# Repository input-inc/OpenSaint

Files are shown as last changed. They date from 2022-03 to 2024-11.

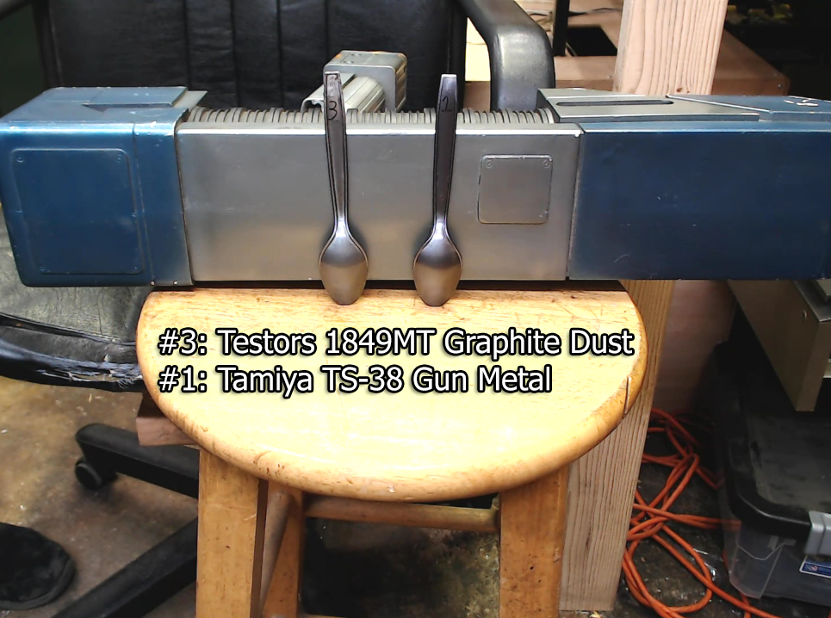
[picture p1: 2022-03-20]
J5 Project/Current CAD/Resources/Manufacturing & Helpful Info/J5 Paint (002).png

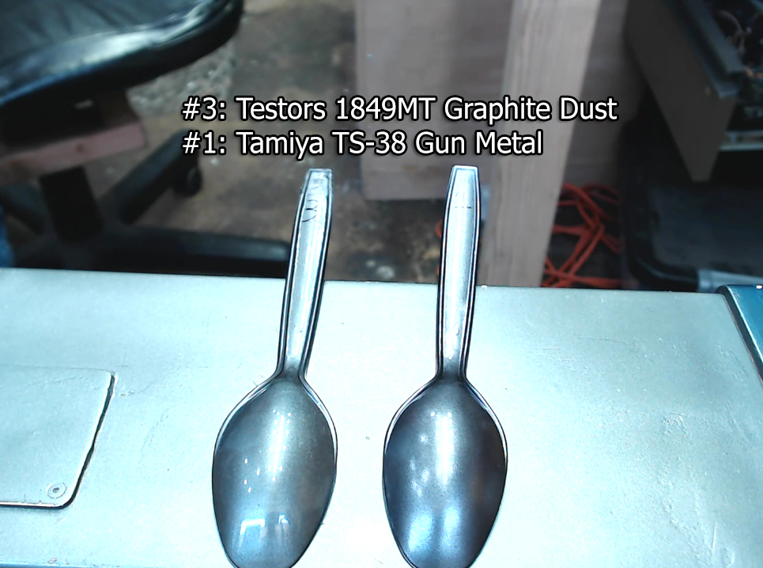
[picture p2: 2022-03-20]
J5 Project/Current CAD/Resources/Manufacturing & Helpful Info/J5 Paint (001).png

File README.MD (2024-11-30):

Input-Inc logo Header
# Welcome to OpenSAINT by Input-Inc.

OpenSAINT is a robotic platform that is a screen accurate replica of a well known movie robot. This platform represents years of mechanical design and collaboration by the Input-Inc. team. Except where noted, it is not affiliated with any persons or groups outside of its core team. Please visit our website (www.input-inc.com) for more information. Please familiarize yourself with this document before proceeding. Building a full-size OpenSAINT robot is an expensive, laborious, and time consuming process. It is recommended you have machining experience, and experience building RC controlled systems.

## Help Keep this Project ALIVE!
We've been working on this project for over twenty years, and have countless hours poured into it. We use industrial grade software and tools to bring this project to an international community of builders, and we can only continue our efforts with your help. Through our Patreon we offer several tiers for builders and non-builders alike to support the project. [Check out our Patreon](https://www.patreon.com/inputinc/)

## License Terms & Conditions
These files are provided under a Creative Commons Attribution-NonCommercial-ShareAlike 4.0 International license (included), and as such this information, or derivatives thereof are intended solely for personal use and cannot be used for commercial purposes. Any distributed modifications of this information must be done under the same terms, and include the license of the original work. 

# !! WARNING !!
Before you get started be warned that this robot when built to specification can still be dangerous. Certain safety mechanisms or mechanical considerations have been designed to reduce this risk as much as possible but the design contains multiple high-powered motors, servos, and mechanisms that in their normal operation can injure the operator or bystanders. It is not recommend to run this robot without taking proper precautions to protect those within its field of operation. 

# How to get started

## Getting the current CAD
Before you download the CAD we recommend you read through our [CAD Releases](https://github.com/input-inc/OpenSaint/wiki/CAD-Releases) document. This will give you more information on our release schedules, distribution mechanisms, and recommended software. Always be sure you have the newest version of the CAD before building, and always get your CAD from the Input-Inc. GitHub repository or Patreon.

## Downloading the CAD from GitHub
GitHub is a public source control hosting and management platform. We use it to host our public CAD. For those without Git experience we recommend downloading the [Git Desktop](https://desktop.github.com) client, and using that to download the files. This will ensure that the LFS structure of the repository is retained when you download it. You will need at least 10GB of hard drive space available to download the entire CAD. 

**!! Do not use the 'Download ZIP' option in the Code dropdown on the GitHub website. That will not download the file contents !!** 
### GitHub Desktop Steps
1. Download GitHub Desktop for your operating system.
2. Install it. (For macOS open the zip file and drag the application to your `/Applications` folder.)
3. Open GitHub Desktop.
4. Select the `File` menu and select `Clone Repository`.
5. Select the `URL` tab from the dialog.
6. Enter this URL: `https://github.com/input-inc/OpenSaint.git`
7. Choose a location where you want to save the files. **IMPORTANT:** For Windows you must install at the top level of a drive like C:, because the path names will exceed the Windows maximum length if it is installed elsewhere.
8. Click the `Clone` button.
9. Wait for the repository to finish downloading.

### Git Command-line Steps
If you prefer to use the command line it will require current versions of `git` and `git lfs`. Download and install in whatever way is appropriate for your operating system.
1. `git lfs clone <repository URL> <path to save>`

## Reading the CAD

### What software do I need?
#### CAD
These CAD files are provided in SolidWorks format and we **expressly** recommend using SolidWorks to read them as outlined in our [CAD Releases](https://github.com/input-inc/OpenSaint/wiki/CAD-Releases) document. To get SolidWorks:Maker, (an affordable version of SolidWorks) you can follow the steps in our [SolidWorks Guide](https://github.com/input-inc/OpenSaint/wiki/Installing-3DExperience-SolidWorks-for-Makers).

Some software packages like Fusion 360 may only read the solid data from the file and could exclude part configurations or other details. Unless otherwise provided, parts do not include flat patterns specified for sheet metal manufacturing. An understanding of CAD tools will be required to extract usable dimensions and patterns for manufacturing.

#### Markdown
For reading the MD (Markdown) files within the repository on your desktop (you can always read them natively within Git's web interface), you'll need a compatible markdown viewer. Here are some suggestions:

##### macOS
- [The 6 Best Mac Markdown Editors](https://www.makeuseof.com/tag/mac-markdown-editors/)

##### Windows
- [The 4 Best Markdown Editors for Windows](https://www.makeuseof.com/best-markdown-editors-windows/)

## How is the CAD organized
The major sections of the robot are broken into folders and subfolders for sub-assemblies. Part files are named to make locating them within this structure as easy as possible. For example the file named: `[CRDL-COMN-C-COMN-00] Battery box.SLDPRT` , could be found at the following path:

`ROOT > [04 CRDL] Cradle Base > [ COMN] Common > [C] Battery Box > [ COMN] Common`

### Configurations and build options (ex. v1 vs. v2)
Input-Inc. uses a few ways to denote differing configurations of assemblies and part files. For certain parts a SolidWorks configuration is provided to represent earlier valid versions of the part, as we endeavor to retain backwards compatibility wherever possible. Be sure to check the configurations tab in SolidWorks to see the differing versions. For some assemblies a V1 or V2 folder can be found within the folder structure to illustrate differing approaches to building the assembly. Not all versions of all assemblies may be compatible so use caution when deviating from the default configurations.

## What you’ll need
Building OpenSAINT will require a full suite of tools, and in many cases we suggest having machining capabilities yourself to build these parts. It is strongly recommended that you fully train and familiarize yourself with any machine or tool outlined here. We accept no responsibility for injuries sustained or failed parts from improper use of these tools.

### Machines
For these machines we recommend the largest you can afford and realistically own.
- Mill (Bench top or larger)
- Lathe (Capable of cutting metal) (Bench top or larger)
- 3D printer (FDM: 350mm2 minimum recommended, Resin)

### Tools
Fractional and Metric allen wrench sets - Most of the fasteners on OpenSAINT are fractional size socket head cap screws. We recommend a quality set of these that go down to .028” and 0.7mm

## Vendors
Most off-the-shelf parts included in the CAD include part numbers for ease of searching. 

### Fasteners
- [McMaster-Carr](https://www.mcmaster.com) - Unless otherwise specified, most of the fasteners can be found here. 
- [Bolt Depot](https://boltdepot.com)
- [Fastenal](fastenal.com)

### Laser cutting
For laser cut parts we’ve found the following vendors to provide excellent results:

- [SendCutSend](https://sendcutsend.com) - 2D sheet metal, laser cutting, and some bending.
- [OSHCut](https://www.oshcut.com) - 2D sheet metal, laser cutting, and bending
- [Ponoko](https://www.ponoko.com) - Plastics laser cutting

### PCBs
- [JLPCB](https://jlpcb.com)
- [OSH Park](https://oshpark.com)
- [PCBWay](https://pcbway.com)

### Servos
- [Servo City](https://www.servocity.com) - Motors, servos, gears
- [ASME](https://www.aliexpress.com/item/32975864627.html) - Beware knock-offs. This is our recommended vendor.

### 3D Printing
- [CraftCloud](https://craftcloud3d.com) - A large marketplace for 3D printing services.

### Other Vendors
- [Bearings Direct](https://bearingsdirect.com)
- [MetalsDepot](https://www.metalsdepot.com)

## Where to get parts
- Part runs - Occasionally Input-Inc. members will have parts for sale, or do parts runs. Visit our [Facebook](https://www.facebook.com/groups/inputinc) and check the announcements for parts runs. We do our best to ensure fit and compatibility but you may still need to make adjustments on stuff.
- [OpenSAINT part Inventory](https://docs.google.com/spreadsheets/d/1wjoVz0FKgDMVw29Vhd8r6FyhR2xi7lMMy8atvSe49dA/edit?usp=sharing) - [Ramon](ryvarra@cyberantics.net) has a running inventory of parts from previous runs and general collecting. Check the list and contact through the Facebook group or by email to make a purchase. Keep in mind that inventory purchases are limited to Patreon Builder/Pro Builder members.

## Community resources
Join us on our Facebook group, and always be on the lookout for build videos.
- [Facebook](https://www.facebook.com/groups/inputinc)
- [YouTube](https://www.youtube.com/user/J5GURU)

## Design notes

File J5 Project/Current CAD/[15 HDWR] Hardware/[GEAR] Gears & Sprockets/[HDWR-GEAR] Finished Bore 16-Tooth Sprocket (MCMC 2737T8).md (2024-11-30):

# @
| Attribute | Value |
| ---  | --- |
| Author | hackmancoltaire |
| Date | 09/27/2016 |
| Part Type | Purchased |
| Cost | 31.04 |
| _SW_Last_Saved_With_ | SOLIDWORKS 2024 |
# Stock
| Attribute | Value |
| ---  | --- |
| Description | Finshed Bore 16-Tooth Sprocket (MCMC 2737T8, Stock) |
| Author | hackmancoltaire |
| Date | 09/27/2016 |
| Part Type | Purchased |
| Cost | 31.04 |
# TUPR Neck Drive
| Attribute | Value |
| ---  | --- |
| Description | BORED SPROCKET. 3/16&quot;Keyway, with Set Screws |
| Comment | https://ametric.com/product/59430/25b1612 |
| Author | hackmancoltaire |
| Date | 09/27/2016 |
| Number | 300936 |
| Part Type | Purchased |
| Cost | 31.04 |
# Neck Drive
| Attribute | Value |
| ---  | --- |
| Description | Finshed Bore 16-Tooth Sprocket (MCMC 2737T8, TUPR Neck Drive) |
| Author | hackmancoltaire |
| Date | 09/27/2016 |
| Part Type | Purchased |
| Cost | 31.04 |

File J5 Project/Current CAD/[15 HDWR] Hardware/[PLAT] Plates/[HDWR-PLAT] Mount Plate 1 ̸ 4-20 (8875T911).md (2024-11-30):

# @
| Attribute | Value |
| ---  | --- |
| Project Name |  |
| Description | Mount Plate for 1/4&quot;-20 Thread Size |
| Author | hackmancoltaire |
| Project number |  |
| Date | 10/16/2024 |
| Number | 8875T911 |
| Vendor | McMaster-Carr Supply Company |
| Material | Steel |
| Part Type | Purchased |
| Cost | 1.28/5 |
| _SW_Last_Saved_With_ | SOLIDWORKS 2024 |
# 8875T911
| Attribute | Value |
| ---  | --- |
| Project Name |  |
| Author | hackmancoltaire |
| Project number |  |
| Date | 10/16/2024 |
| Part Type | Purchased |
| Cost | 1.28/5 |

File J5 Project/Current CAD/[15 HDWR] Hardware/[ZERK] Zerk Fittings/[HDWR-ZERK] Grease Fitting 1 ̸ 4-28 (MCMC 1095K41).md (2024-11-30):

# @
| Attribute | Value |
| ---  | --- |
| Project Name |  |
| Description | Zinc-Plated Steel Grease Fitting |
| Author | hackmancoltaire |
| Project number |  |
| Date | 11/09/2024 |
| Vendor | McMaster-Carr Supply Company |
| Material | Steel |
| _SW_Last_Saved_With_ | SOLIDWORKS 2024 |
# Default
| Attribute | Value |
| ---  | --- |
| Project Name |  |
| Author | hackmancoltaire |
| Project number |  |
| Date | 11/09/2024 |

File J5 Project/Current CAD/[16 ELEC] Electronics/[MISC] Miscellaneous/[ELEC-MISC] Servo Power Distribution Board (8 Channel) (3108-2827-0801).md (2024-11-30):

# @
| Attribute | Value |
| ---  | --- |
| Project Name |  |
| Description | Servo Power Distribution Board (8 Channel) |
| Author | hackmancoltaire |
| Project number |  |
| Date | 11/02/2024 |
| Number | 3108-2827-0801 |
| Vendor | GoBuilda |
| _SW_Last_Saved_With_ | SOLIDWORKS 2024 |
# Default
| Attribute | Value |
| ---  | --- |
| Project Name |  |
| Author | hackmancoltaire |
| Project number |  |
| Date | 11/02/2024 |
| Vendor | GoBuilda |

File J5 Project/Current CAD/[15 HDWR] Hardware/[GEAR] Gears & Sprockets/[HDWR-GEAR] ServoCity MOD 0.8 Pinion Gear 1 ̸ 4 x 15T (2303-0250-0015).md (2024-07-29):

# @
| Attribute | Value |
| ---  | --- |
| Project Name |  |
| Description | 2303 Series Steel, MOD 0.8 Pinion Gear (1/4&quot; Round Bore, 15 Tooth) |
| Author | hackmancoltaire |
| Revision | ANY |
| Project number |  |
| Date | 07/28/2024 |
| Number | 2303-0250-0015 |
| Vendor | ServoCity |
| Part Type | Purchased |
| Cost | 9.99 |
| _SW_Last_Saved_With_ | SOLIDWORKS 2024 |
# Default
| Attribute | Value |
| ---  | --- |
| Project Name |  |
| Author | hackmancoltaire |
| Project number |  |
| Date | 07/28/2024 |
| Vendor | ServoCity |
| Part Type | Purchased |
| Cost | 9.99 |

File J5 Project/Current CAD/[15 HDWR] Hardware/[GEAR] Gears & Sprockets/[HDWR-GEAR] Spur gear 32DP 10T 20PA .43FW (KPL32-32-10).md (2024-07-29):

# @
| Attribute | Value |
| ---  | --- |
| Project Name |  |
| Description | 10T, 0.125&quot; (1/8) Bore 32P Shaft Mount Pinion Gear (Steel) |
| Author | hackmancoltaire |
| Project number |  |
| Date | 06/22/2024 |
| Number | KPL32-32-10 |
| Part Type | Purchased |
| Cost | 5.99 |
| _SW_Last_Saved_With_ | SOLIDWORKS 2024 |
# Default
| Attribute | Value |
| ---  | --- |
| Project Name |  |
| Author | hackmancoltaire |
| Project number |  |
| Date | 06/22/2024 |
| Part Type | Purchased |
| Cost | 5.99 |

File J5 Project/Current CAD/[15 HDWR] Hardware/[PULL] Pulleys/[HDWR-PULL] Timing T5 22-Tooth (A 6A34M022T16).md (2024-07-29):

# @
| Attribute | Value |
| ---  | --- |
| Author | hackmancoltaire |
| Date | 11/30/2019 |
| _SW_Last_Saved_With_ | SOLIDWORKS 2024 |
# ARM Hug Output
| Attribute | Value |
| ---  | --- |
| Author | hackmancoltaire |
| Date | 11/30/2019 |
# ARM Hug Servo
| Attribute | Value |
| ---  | --- |
| Author | hackmancoltaire |
| Date | 11/30/2019 |

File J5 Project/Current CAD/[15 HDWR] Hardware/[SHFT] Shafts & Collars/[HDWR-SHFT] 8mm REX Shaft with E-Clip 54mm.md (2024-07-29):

# @
| Attribute | Value |
| ---  | --- |
| Project Name |  |
| Description | 8mm REX™ Shaft with E-Clip (Stainless Steel, 54mm Length) |
| Author | hackmancoltaire |
| Revision | ANY |
| Project number |  |
| Date | 07/14/2024 |
| Number | 2106-4008-0540 |
| Part Type | Purchased |
| Cost | 3.79 |
| _SW_Last_Saved_With_ | SOLIDWORKS 2024 |
# Default
| Attribute | Value |
| ---  | --- |
| Project Name |  |
| Author | hackmancoltaire |
| Project number |  |
| Date | 07/14/2024 |
| Part Type | Purchased |
| Cost | 3.79 |

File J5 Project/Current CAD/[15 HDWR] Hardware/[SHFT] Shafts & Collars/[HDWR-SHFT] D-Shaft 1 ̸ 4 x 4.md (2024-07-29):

# @
| Attribute | Value |
| ---  | --- |
| Project Name |  |
| Description | 1/4&quot; D-Shaft (Stainless Steel, 4&quot; Length) |
| Author | hackmancoltaire |
| Project number |  |
| Date | 06/23/2024 |
| Number | 2101-1250-0400 |
| Vendor | ServoCity |
| Part Type | Purchased |
| Cost | 3.89 |
| _SW_Last_Saved_With_ | SOLIDWORKS 2024 |
# Default
| Attribute | Value |
| ---  | --- |
| Project Name |  |
| Author | hackmancoltaire |
| Project number |  |
| Date | 06/23/2024 |
| Vendor | ServoCity |
| Part Type | Purchased |
| Cost | 3.89 |

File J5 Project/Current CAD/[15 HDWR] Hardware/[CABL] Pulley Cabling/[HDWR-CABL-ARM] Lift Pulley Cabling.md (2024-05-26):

# @
| Attribute | Value |
| ---  | --- |
| Description | 18-8 Stainless Steel Corrosion-Resistant Wire Rope |
| Author | hackmancoltaire |
| Date | 02/21/2016 |
| Number | 3461T474 |
| Part Type | Purchased |
| _SW_Last_Saved_With_ | SOLIDWORKS 2024 |
# Default
| Attribute | Value |
| ---  | --- |
| Author | hackmancoltaire |
| Date | 02/21/2016 |
| Part Type | Purchased |

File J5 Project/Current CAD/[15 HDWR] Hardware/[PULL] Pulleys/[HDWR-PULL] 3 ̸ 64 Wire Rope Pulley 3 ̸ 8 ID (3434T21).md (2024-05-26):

# @
| Attribute | Value |
| ---  | --- |
| Description | Pulley for Wire Rope |
| Author | hackmancoltaire |
| Date | 11/05/2023 |
| Number | 3434T21 |
| Vendor | McMaster-Carr Supply Company |
| Material | Steel |
| Part Type | Purchased |
| Cost | 4.90 |
| _SW_Last_Saved_With_ | SOLIDWORKS 2024 |
# 3434T21
| Attribute | Value |
| ---  | --- |
| Author | hackmancoltaire |
| Date | 11/05/2023 |
| Part Type | Purchased |
| Cost | 4.90 |

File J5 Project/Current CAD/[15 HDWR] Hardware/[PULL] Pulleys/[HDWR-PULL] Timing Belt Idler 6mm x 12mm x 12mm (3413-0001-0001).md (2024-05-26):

# @
| Attribute | Value |
| ---  | --- |
| Description | Acetal Timing Belt Idler |
| Author | hackmancoltaire |
| Revision | ANY |
| Date | 11/28/2022 |
| Number | 3413-0001-0001 |
| Part Type | Purchased |
| Cost | 2.99/2 |
| _SW_Last_Saved_With_ | SOLIDWORKS 2024 |
# Default
| Attribute | Value |
| ---  | --- |
| Author | hackmancoltaire |
| Date | 11/28/2022 |
| Part Type | Purchased |
| Cost | 2.99/2 |

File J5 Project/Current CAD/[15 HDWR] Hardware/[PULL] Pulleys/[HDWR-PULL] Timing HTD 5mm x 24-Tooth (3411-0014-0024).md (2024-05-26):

# @
| Attribute | Value |
| ---  | --- |
| Description | 5mm HTD Pitch Aluminum Hub Mount Timing Belt Pulley (14mm Bore, 24 Tooth) |
| Author | hackmancoltaire |
| Date | 11/28/2022 |
| Number | 3411-0014-0024 |
| Part Type | Purchased |
| Cost | 7.99 |
| _SW_Last_Saved_With_ | SOLIDWORKS 2024 |
# Default
| Attribute | Value |
| ---  | --- |
| Author | hackmancoltaire |
| Date | 11/28/2022 |
| Part Type | Purchased |
| Cost | 7.99 |

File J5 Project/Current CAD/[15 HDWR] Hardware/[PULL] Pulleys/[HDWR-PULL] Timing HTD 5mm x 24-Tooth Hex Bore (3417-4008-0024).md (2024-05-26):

# @
| Attribute | Value |
| ---  | --- |
| Description | 5mm HTD Pitch Set Screw Pinion Timing Belt Pulley (8mm REX Bore, 24 Tooth) |
| Author | hackmancoltaire |
| Date | 11/29/2022 |
| Number | 3417-4008-0024 |
| Part Type | Purchased |
| Cost | 8.99 |
| _SW_Last_Saved_With_ | SOLIDWORKS 2024 |
# Default
| Attribute | Value |
| ---  | --- |
| Author | hackmancoltaire |
| Date | 11/29/2022 |
| Part Type | Purchased |
| Cost | 8.99 |

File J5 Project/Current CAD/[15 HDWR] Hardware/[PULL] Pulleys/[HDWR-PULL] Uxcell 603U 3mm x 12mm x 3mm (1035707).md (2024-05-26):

# @
| Attribute | Value |
| ---  | --- |
| Project Name |  |
| Description | Uxcell 603 U Groove Ball Track Guide Bearing 3x10x3mm Double Metal Shielded (GCr15) Chrome Steel Bearing |
| Author | hackmancoltaire |
| Project number |  |
| Date | 04/14/2024 |
| Number | 1035707 |
| Part Type | Purchased |
| Cost | 6.08/2 |
| _SW_Last_Saved_With_ | SOLIDWORKS 2024 |
# Default
| Attribute | Value |
| ---  | --- |
| Project Name |  |
| Author | hackmancoltaire |
| Project number |  |
| Date | 04/14/2024 |
| Part Type | Purchased |
| Cost | 6.08/2 |

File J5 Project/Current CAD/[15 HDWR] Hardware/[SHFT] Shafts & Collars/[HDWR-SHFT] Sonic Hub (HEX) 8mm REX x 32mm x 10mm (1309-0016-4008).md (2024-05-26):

# @
| Attribute | Value |
| ---  | --- |
| Description | Sonic Hub (8mm REX Bore) |
| Author | hackmancoltaire |
| Date | 11/28/2022 |
| Number | 1309-0016-4008 |
| _SW_Last_Saved_With_ | SOLIDWORKS 2024 |
# Stock
| Attribute | Value |
| ---  | --- |
| Author | hackmancoltaire |
| Date | 11/28/2022 |
# Arm - Inner
| Attribute | Value |
| ---  | --- |
| Author | hackmancoltaire |
| Date | 11/28/2022 |
# Arm - Outer
| Attribute | Value |
| ---  | --- |
| Author | hackmancoltaire |
| Date | 11/28/2022 |

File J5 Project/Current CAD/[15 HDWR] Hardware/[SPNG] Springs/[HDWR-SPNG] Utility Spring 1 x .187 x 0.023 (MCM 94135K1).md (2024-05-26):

# @
| Attribute | Value |
| ---  | --- |
| Project Name |  |
| Description | 302 Stainless Steel Corrosion-Resistant Extension Spring |
| Author | hackmancoltaire |
| Project number |  |
| Date | 04/28/2024 |
| Number | 94135K1 |
| Vendor | McMaster-Carr Supply Company |
| Material | 302 Stainless Steel |
| _SW_Last_Saved_With_ | SOLIDWORKS 2024 |
# 94135K1
| Attribute | Value |
| ---  | --- |
| Project Name |  |
| Author | hackmancoltaire |
| Project number |  |
| Date | 04/28/2024 |

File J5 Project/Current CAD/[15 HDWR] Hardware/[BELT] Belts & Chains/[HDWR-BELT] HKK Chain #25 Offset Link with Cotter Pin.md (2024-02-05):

# @
| Attribute | Value |
| ---  | --- |
| Project Name |  |
| Description | Adding-and-Connecting Link for ANSI Number 25-SS Single Strand Corrosion-Resistant Roller Chain |
| Author | hackmancoltaire |
| Project number |  |
| Date | 01/14/2024 |
| Number | 6264K3 |
| Vendor | McMaster-Carr Supply Company |
| Material | 304 Stainless Steel |
| _SW_Last_Saved_With_ | SOLIDWORKS 2024 |
# 6264K3
| Attribute | Value |
| ---  | --- |
| Project Name |  |
| Author | hackmancoltaire |
| Project number |  |
| Date | 01/14/2024 |

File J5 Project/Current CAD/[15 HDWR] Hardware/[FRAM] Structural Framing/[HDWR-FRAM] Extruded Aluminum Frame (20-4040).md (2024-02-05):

# @
| Attribute | Value |
| ---  | --- |
| Project Name |  |
| Description | 40mm X 40mm T-Slotted Profile - Eight Open T-Slots |
| Author | hackmancoltaire |
| Project number |  |
| Date | 02/04/2024 |
| Number | 20-4040 |
| Part Type | Purchased |
| Cost | .0285/mm |
| _SW_Last_Saved_With_ | SOLIDWORKS 2024 |
# Default
| Attribute | Value |
| ---  | --- |
| Project Name |  |
| Author | hackmancoltaire |
| Project number |  |
| Date | 02/04/2024 |
| Part Type | Purchased |
| Cost | .0285/mm |

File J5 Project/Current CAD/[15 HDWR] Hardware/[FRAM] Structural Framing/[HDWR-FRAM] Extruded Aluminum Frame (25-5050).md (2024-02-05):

# @
| Attribute | Value |
| ---  | --- |
| Project Name |  |
| Description | 50mm X 50mm T-Slotted Profile - Eight Open T-Slots |
| Author | hackmancoltaire |
| Project number |  |
| Date | 01/07/2024 |
| Number | 25-5050 |
| Part Type | Purchased |
| Cost | $0.0330/mm |
| _SW_Last_Saved_With_ | SOLIDWORKS 2024 |
# 111.125mm
| Attribute | Value |
| ---  | --- |
| Project Name |  |
| Author | hackmancoltaire |
| Project number |  |
| Date | 01/07/2024 |
| Part Type | Purchased |
| Cost | $0.0330/mm |
# 51.7525mm
| Attribute | Value |
| ---  | --- |
| Project Name |  |
| Author | hackmancoltaire |
| Project number |  |
| Date | 01/07/2024 |
| Part Type | Purchased |
| Cost | $0.0330/mm |
# 93.6625mm
| Attribute | Value |
| ---  | --- |
| Project Name |  |
| Author | hackmancoltaire |
| Project number |  |
| Date | 01/07/2024 |
| Part Type | Purchased |
| Cost | $0.0330/mm |
# 95.25mm
| Attribute | Value |
| ---  | --- |
| Author | hackmancoltaire |
| Date | 01/07/2024 |
| Part Type | Purchased |
| Cost | $0.0330/mm |
# 52.4002mm
| Attribute | Value |
| ---  | --- |
| Author | hackmancoltaire |
| Date | 01/07/2024 |
| Part Type | Purchased |
| Cost | $0.0330/mm |
# 104.14mm
| Attribute | Value |
| ---  | --- |
| Author | hackmancoltaire |
| Date | 01/07/2024 |
| Part Type | Purchased |
| Cost | $0.0330/mm |
# 49.149mm
| Attribute | Value |
| ---  | --- |
| Author | hackmancoltaire |
| Date | 01/07/2024 |
| Part Type | Purchased |
| Cost | $0.0330/mm |

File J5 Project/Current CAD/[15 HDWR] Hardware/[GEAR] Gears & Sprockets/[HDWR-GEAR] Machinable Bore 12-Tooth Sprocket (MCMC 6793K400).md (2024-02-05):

# @
| Attribute | Value |
| ---  | --- |
| Description | McMaster-Carr ANSI 25 Chain, 12 Teeth, for 1/4&quot; Shaft Diameter |
| Author | SixWingedFreak |
| Date | 09/20/2016 |
| Number | 6793K400 |
| _SW_Last_Saved_With_ | SOLIDWORKS 2024 |
# Stock
| Attribute | Value |
| ---  | --- |
| Author | SixWingedFreak |
| Date | 09/20/2016 |
# TUPR Neck Drive
| Attribute | Value |
| ---  | --- |
| Author | SixWingedFreak |
| Date | 09/20/2016 |

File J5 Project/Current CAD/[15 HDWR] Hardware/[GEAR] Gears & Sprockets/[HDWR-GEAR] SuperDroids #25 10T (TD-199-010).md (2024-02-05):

# @
| Attribute | Value |
| ---  | --- |
| Project Name |  |
| Description | Steel D-Shaft Sprocket for #25 Pitch Chain - 10 Teeth |
| Author | hackmancoltaire |
| Project number |  |
| Date | 01/10/2024 |
| Number | TD-199-010 |
| Part Type | Purchased |
| Cost | 8.64 |
| _SW_Last_Saved_With_ | SOLIDWORKS 2024 |
# 25-0.25P1ST10T10SN3.0H2.0L0.1250N
| Attribute | Value |
| ---  | --- |
| Project Name |  |
| Author | hackmancoltaire |
| Project number |  |
| Date | 01/10/2024 |
| Part Type | Purchased |
| Cost | 8.64 |

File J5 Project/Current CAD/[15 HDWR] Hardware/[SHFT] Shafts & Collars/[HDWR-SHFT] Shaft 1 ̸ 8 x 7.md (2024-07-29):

# @
| Attribute | Value |
| ---  | --- |
| Project Name |  |
| Description | 0.125” (1/8”) x 7.00” Stainless Steel Precision Shafting |
| Author | hackmancoltaire |
| Project number |  |
| Date | 06/19/2024 |
| Number | 634126 |
| Part Type | Purchased |
| Cost | 1.19 |
| _SW_Last_Saved_With_ | SOLIDWORKS 2024 |
# Default
| Attribute | Value |
| ---  | --- |
| Project Name |  |
| Author | hackmancoltaire |
| Project number |  |
| Date | 06/19/2024 |
| Part Type | Purchased |
| Cost | 1.19 |

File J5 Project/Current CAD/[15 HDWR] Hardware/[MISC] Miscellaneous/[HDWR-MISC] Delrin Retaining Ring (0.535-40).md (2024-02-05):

# @
| Attribute | Value |
| ---  | --- |
| Project Name |  |
| Description | Retaining Ring 0.535-40 Thread (Pack Of 10) |
| Author | hackmancoltaire |
| Project number |  |
| Date | 01/29/2024 |
| Number | RR05-P10 |
| Part Type | Purchased |
| Cost | 38.50/10 |
| _SW_Last_Saved_With_ | SOLIDWORKS 2024 |
# Default
| Attribute | Value |
| ---  | --- |
| Project Name |  |
| Author | hackmancoltaire |
| Project number |  |
| Date | 01/29/2024 |
| Part Type | Purchased |
| Cost | 38.50/10 |
# Simplified
| Attribute | Value |
| ---  | --- |
| Project Name |  |
| Author | hackmancoltaire |
| Project number |  |
| Date | 01/29/2024 |
| Part Type | Purchased |
| Cost | 38.50/10 |

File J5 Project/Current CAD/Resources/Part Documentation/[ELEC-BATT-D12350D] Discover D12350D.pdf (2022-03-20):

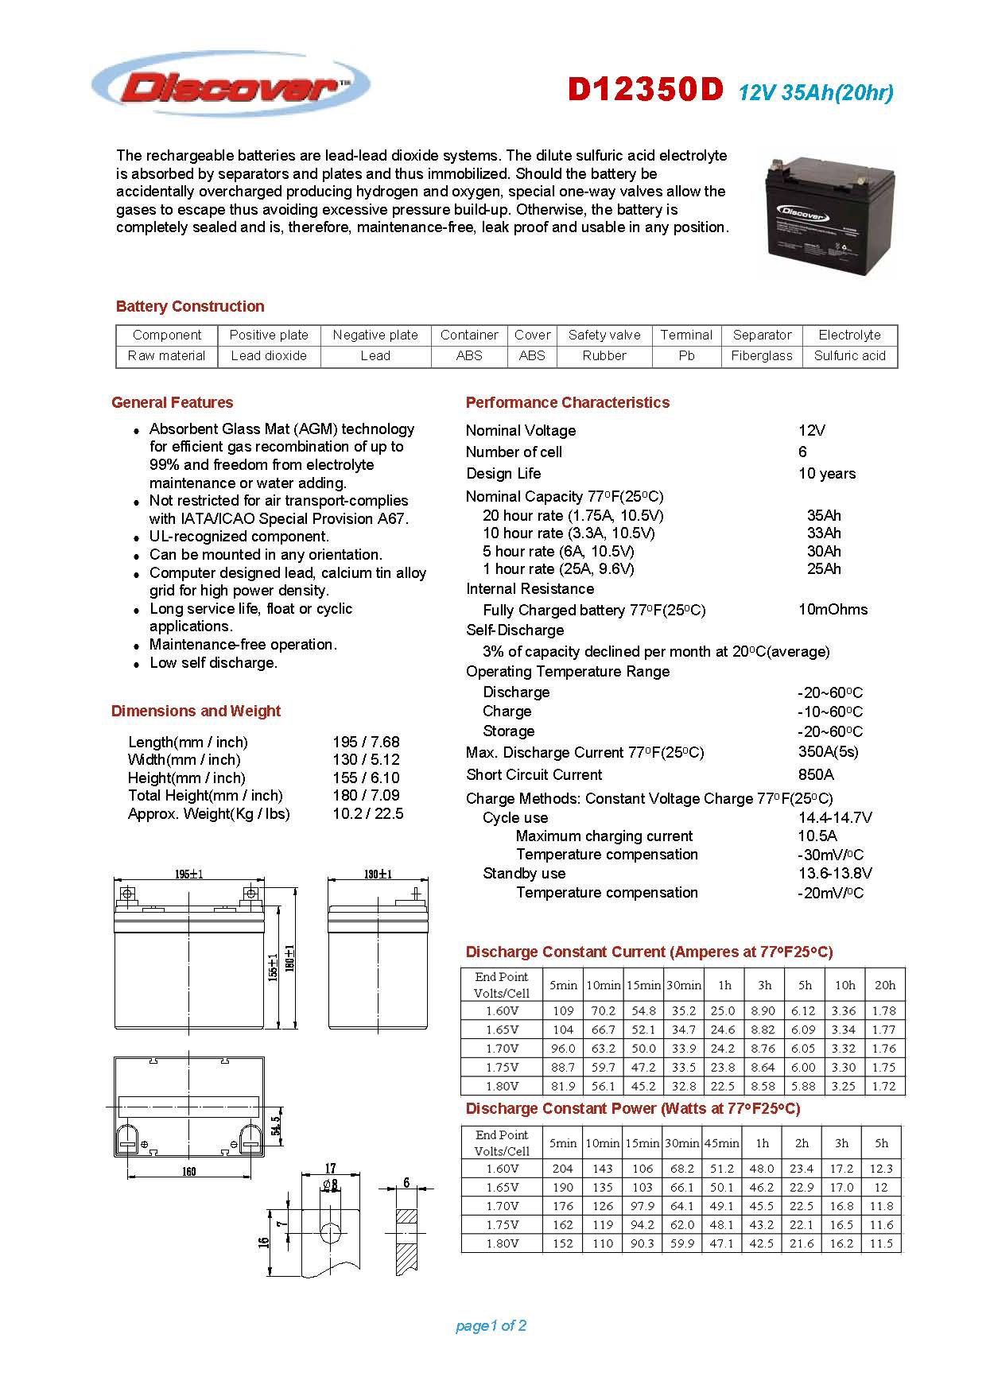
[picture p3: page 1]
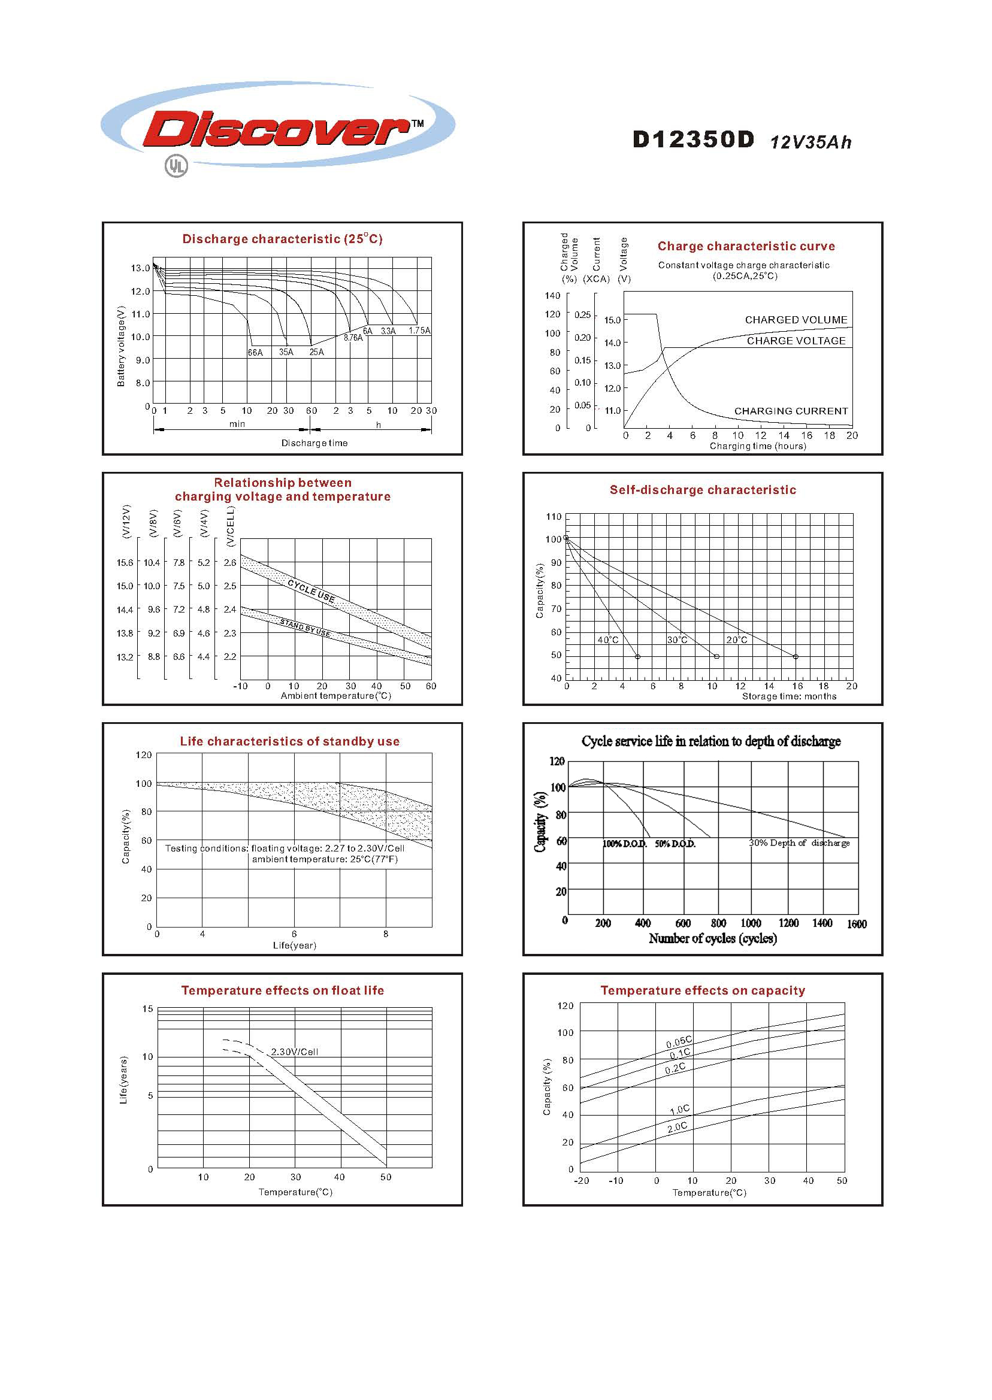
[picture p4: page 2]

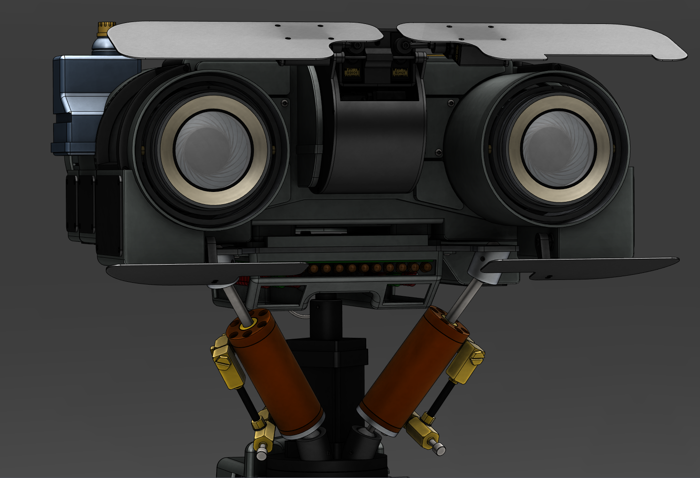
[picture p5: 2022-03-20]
J5 Project/Current CAD/Resources/Renders & Screenshots/Head01.png

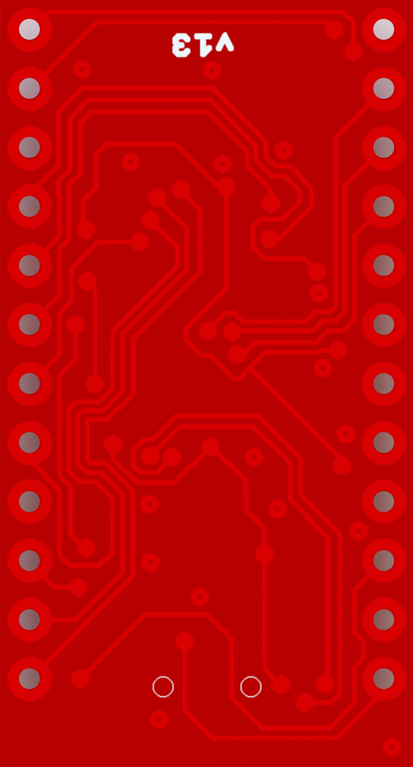
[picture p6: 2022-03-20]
J5 Project/Current CAD/Resources/Decals/PCBs/Arduino Pro Micro PCB (Bottom).png

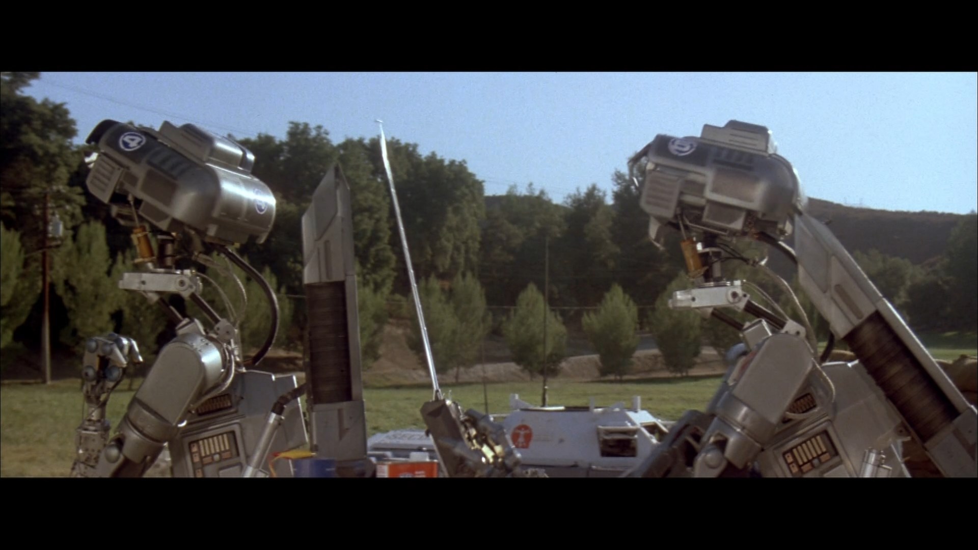
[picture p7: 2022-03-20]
J5 Project/Current CAD/[13 ACC] Accessory/[LASR] Laser/[ MSTR] Master/Reference/Laser Reference 32.jpg

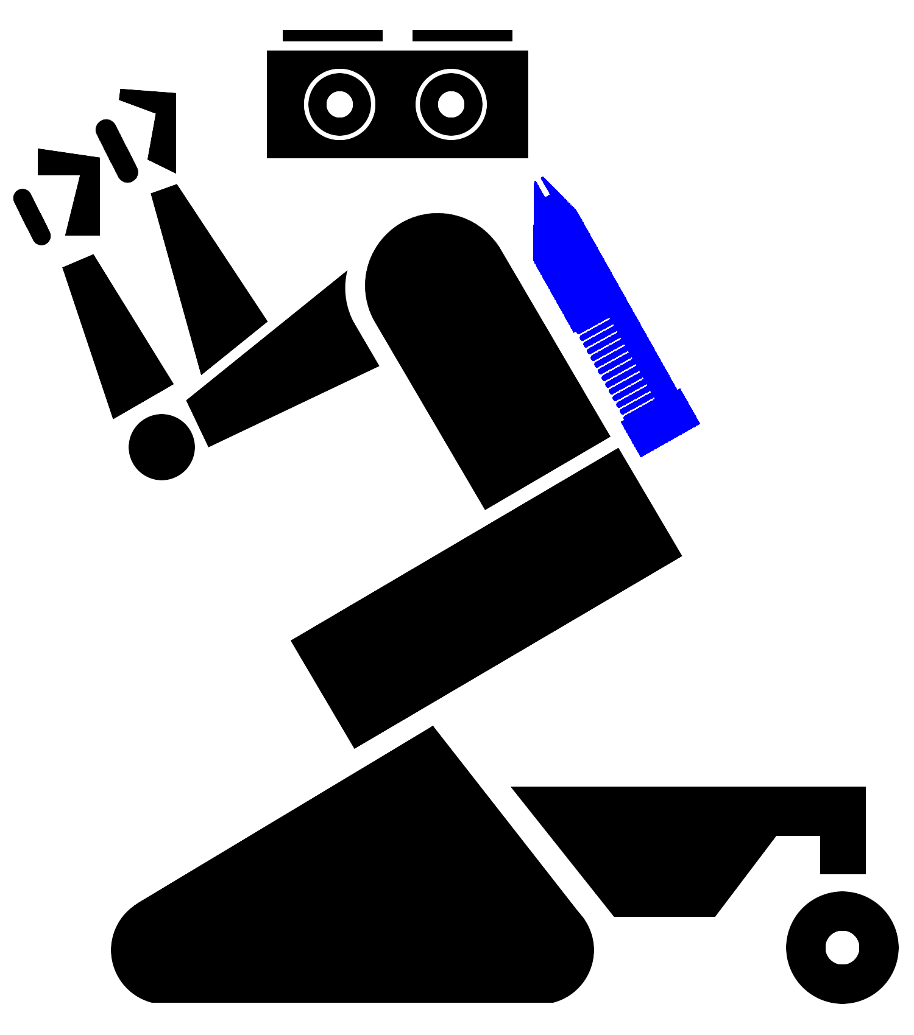
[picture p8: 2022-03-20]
J5 Project/Current CAD/Resources/SolidWorks Settings & Tools/Drawing Resources/Art/Zones/ACC.png

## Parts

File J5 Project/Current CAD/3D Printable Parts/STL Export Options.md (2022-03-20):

# 
| Attribute | Value |
| ---  | --- |
| Author | SixWingedFreak |
| Width | 944 |
| Height | 810 |
| Color Depth | 8 |

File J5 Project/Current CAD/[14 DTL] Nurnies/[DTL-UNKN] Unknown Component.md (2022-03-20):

# @
| Attribute | Value |
| ---  | --- |
| Author | SixWingedFreak |
| Date | 05/19/2015 |
# Chamfered Corners
| Attribute | Value |
| ---  | --- |
| Author | SixWingedFreak |
| Date | 05/19/2015 |
# Rounded Corners
| Attribute | Value |
| ---  | --- |
| Author | SixWingedFreak |
| Date | 05/19/2015 |

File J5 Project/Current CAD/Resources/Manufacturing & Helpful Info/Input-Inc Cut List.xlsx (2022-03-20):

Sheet: Standard
INPUT-INC CUT LIST
DESCRIPTION | SIZE | CUTS | TOTAL REQUIRED | PURCHASE | BREAKDOWN
90° Angle Steel | 1¼" x 1¼" | 11.25'' | 11.25'' | 1' x1 | N/A
 | ¾" x ¾" | 22.16'' | 44.32'' | 6' x1 | N/A
 |  | 22.16''
 | ½" x ½" | 13.8'' | 89.155'' | 3' x1 6' x1 | 3' 4.965" x2 3.875 x2 1.6875" x1
 |  | 13.8''
 |  | 10.25''
 |  | 10.25''
 |  | 5''
 |  | 5''
 |  | 5''
 |  | 5'' |  |  | 6' 13.8" x2 10.25" x2 5" x4 1.6875" x1
 |  | 4.965''
 |  | 4.965''
 |  | 3.875''
 |  | 3.875''
 |  | 1.6875''
 |  | 1.6875''
90° Angle Aluminum | ¾" x ¾" | 5'' | 14.75'' | 3' x1 | N/A
 |  | 5''
 |  | 2''
 |  | 2''
 |  | 0.375''
 |  | 0.375''

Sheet: Terry
INPUT-INC CUT LIST (TERRY)
DESCRIPTION | SIZE | CUTS | TOTAL REQUIRED | PURCHASE | BREAKDOWN
90° Angle Steel | 1¼" x 1¼" | 11.25'' | 11.25'' | 1' x1 | N/A
 | ¾" x ¾" | 22.16'' | 59.07'' | 6' x1 | N/A
 |  | 22.16''
 |  | 5''
 |  | 5''
 |  | 2''
 |  | 2''
 |  | 0.375''
 |  | 0.375''
 | ½" x ½" | 13.8'' | 89.155'' | 3' x1 6' x1 | 3' 4.965" x2 3.875 x2 1.6875" x1
 |  | 13.8''
 |  | 10.25''
 |  | 10.25''
 |  | 5''
 |  | 5''
 |  | 5''
 |  | 5'' |  |  | 6' 13.8" x2 10.25" x2 5" x4 1.6875" x1
 |  | 4.965''
 |  | 4.965''
 |  | 3.875''
 |  | 3.875''
 |  | 1.6875''
 |  | 1.6875''

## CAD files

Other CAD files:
J5 Project/Current CAD/[00 FULL] Complete Assembly/[ COMN] Common/[FULL-COMN] Lower Half.SLDASM
J5 Project/Current CAD/[00 FULL] Complete Assembly/[FULL] Complete Assembly.SLDASM
J5 Project/Current CAD/[01 HEAD] Head (UNFINISHED)/[ COVR] Coverings/[MIL1] Facemask & Mouthguard/[HEAD-COVR-MIL1] Facemask & Mouthguard Assembly.SLDASM
J5 Project/Current CAD/[01 HEAD] Head (UNFINISHED)/[A] Shell/[HEAD-A] Top Shell.SLDASM
J5 Project/Current CAD/[01 HEAD] Head (UNFINISHED)/[B] Eye/[A] Wollensak Raptar 209mm Copy Lens/[HEAD-B-A] Wollensak Raptar 209mm Copy Lens.SLDASM
J5 Project/Current CAD/[01 HEAD] Head (UNFINISHED)/[B] Eye/[C] Iris Rotator/[HEAD-B-C] Iris Rotator.SLDASM
J5 Project/Current CAD/[01 HEAD] Head (UNFINISHED)/[B] Eye/[D] XY Eye Articulator/[HEAD-B-D-R] XY Eye Articulator (Right).SLDASM
J5 Project/Current CAD/[01 HEAD] Head (UNFINISHED)/[B] Eye/[HEAD-B] Eye.SLDASM
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

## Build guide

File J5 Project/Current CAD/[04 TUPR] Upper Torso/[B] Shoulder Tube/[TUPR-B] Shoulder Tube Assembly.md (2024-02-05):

# @
| Attribute | Value |
| ---  | --- |
| Author | SixWingedFreak |
| Date | 07/31/2016 |
| _SW_Last_Saved_With_ | SOLIDWORKS 2024 |
# Flipped motor nuts (Screen Accurate)
| Attribute | Value |
| ---  | --- |
| Author | SixWingedFreak |
| Date | 07/31/2016 |
# Symmetric Motor Nuts
| Attribute | Value |
| ---  | --- |
| Author | SixWingedFreak |
| Date | 07/31/2016 |

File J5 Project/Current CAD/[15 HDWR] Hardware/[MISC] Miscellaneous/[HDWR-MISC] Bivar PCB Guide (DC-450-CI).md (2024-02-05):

# @
| Attribute | Value |
| ---  | --- |
| Project Name |  |
| Description | Circuit Board Hardware, PCB Card Guides, DC |
| Author | hackmancoltaire |
| Project number |  |
| Date | 01/26/2024 |
| Number | DC-450-CI |
| Part Type | Purchased |
| _SW_Last_Saved_With_ | SOLIDWORKS 2024 |
# Default
| Attribute | Value |
| ---  | --- |
| Project Name |  |
| Author | hackmancoltaire |
| Project number |  |
| Date | 01/26/2024 |
| Part Type | Purchased |

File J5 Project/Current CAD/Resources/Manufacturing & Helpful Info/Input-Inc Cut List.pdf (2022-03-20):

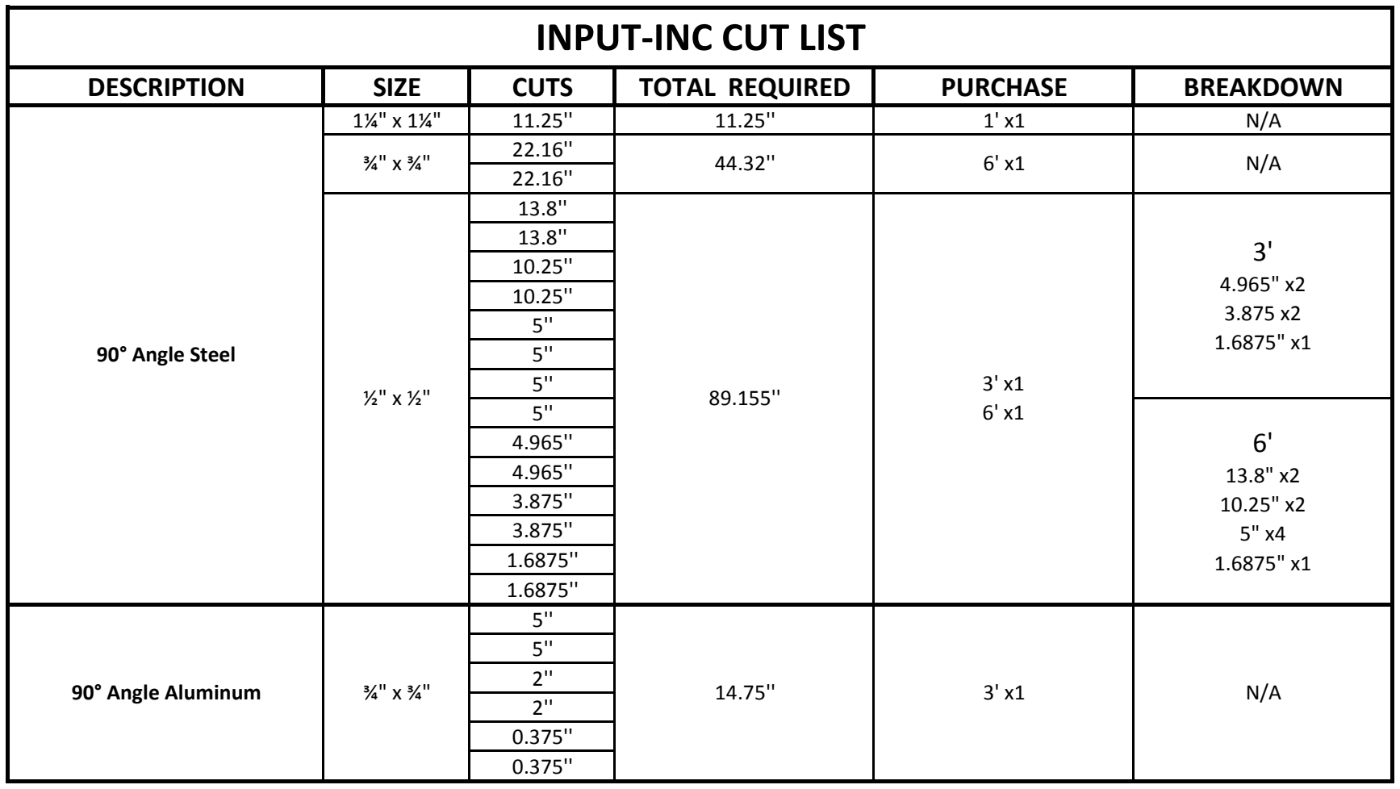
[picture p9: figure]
INPUT-INC CUT LIST; 90° Angle Steel

DESCRIPTION | SIZE | CUTS | TOTAL REQUIRED | PURCHASE | BREAKDOWN
90° Angle Aluminum | ¾" x ¾" | 14.75'' | 3' x1

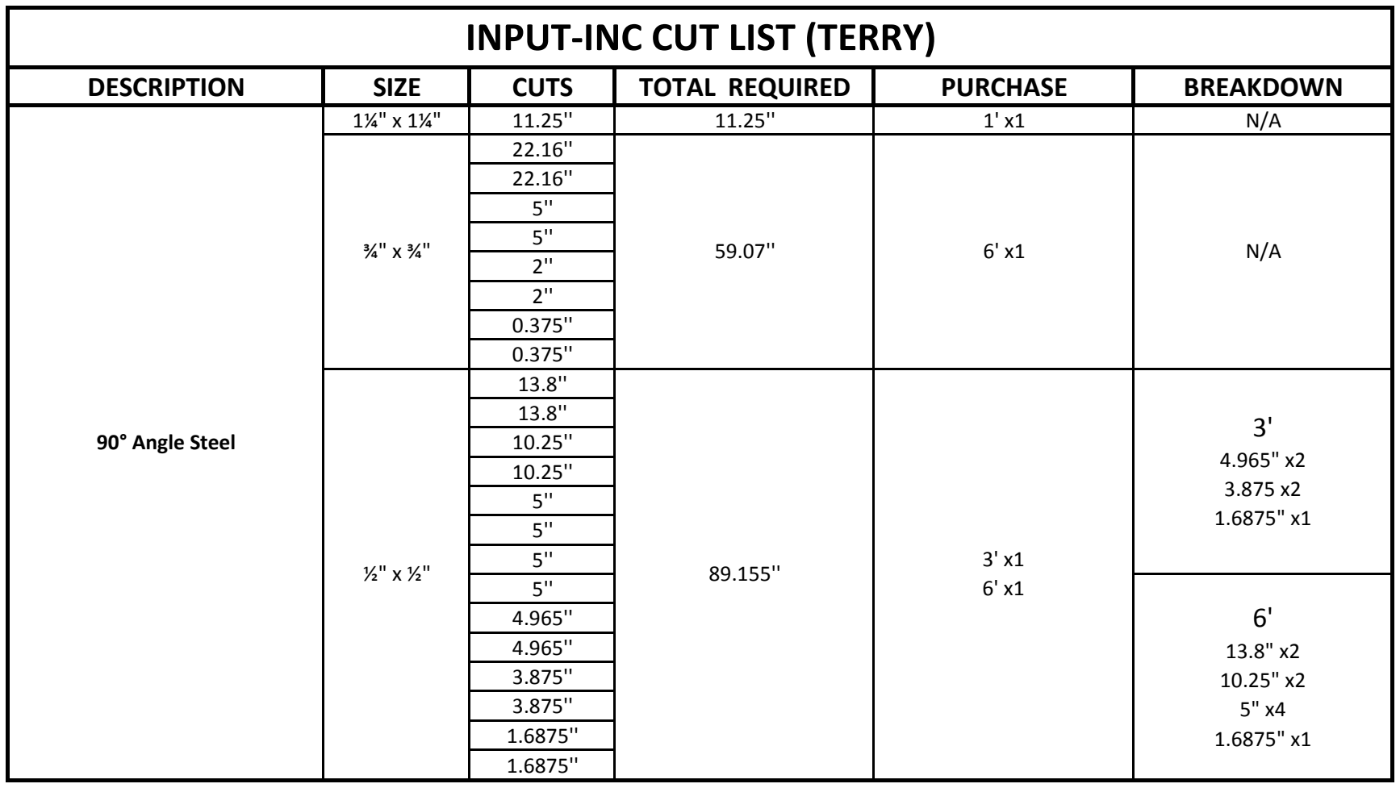
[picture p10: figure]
INPUT-INC CUT LIST (TERRY); 90° Angle Steel

DESCRIPTION | SIZE | CUTS | TOTAL REQUIRED | PURCHASE | BREAKDOWN

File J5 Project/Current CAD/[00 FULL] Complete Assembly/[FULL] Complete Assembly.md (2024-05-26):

# @
| Attribute | Value |
| ---  | --- |
| Author | hackmancoltaire |
| Date | 12/22/2022 |
| _SW_Last_Saved_With_ | SOLIDWORKS 2024 |
# Default
| Attribute | Value |
| ---  | --- |
| Author | hackmancoltaire |
| Date | 12/22/2022 |

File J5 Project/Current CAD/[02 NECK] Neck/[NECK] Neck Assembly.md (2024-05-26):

# @
| Attribute | Value |
| ---  | --- |
| Author | SixWingedFreak |
| Date | 05/22/2015 |
| _SW_Last_Saved_With_ | SOLIDWORKS 2024 |
# V2
| Attribute | Value |
| ---  | --- |
| Author | SixWingedFreak |
| Date | 05/22/2015 |
# V1
| Attribute | Value |
| ---  | --- |
| Author | SixWingedFreak |
| Date | 05/22/2015 |
# V3
| Attribute | Value |
| ---  | --- |
| Author | SixWingedFreak |
| Date | 05/22/2015 |

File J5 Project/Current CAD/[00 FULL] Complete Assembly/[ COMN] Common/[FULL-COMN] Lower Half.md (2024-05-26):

# @
| Attribute | Value |
| ---  | --- |
| Author | SixWingedFreak |
| Date | 03/16/2016 |
| _SW_Last_Saved_With_ | SOLIDWORKS 2024 |
# Default
| Attribute | Value |
| ---  | --- |
| Author | SixWingedFreak |
| Date | 03/16/2016 |

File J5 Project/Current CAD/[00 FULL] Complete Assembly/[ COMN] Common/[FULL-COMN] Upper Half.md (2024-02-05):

# @
| Attribute | Value |
| ---  | --- |
| Author | SixWingedFreak |
| Date | 08/01/2016 |
| _SW_Last_Saved_With_ | SOLIDWORKS 2024 |
# Default
| Attribute | Value |
| ---  | --- |
| Author | SixWingedFreak |
| Date | 08/01/2016 |

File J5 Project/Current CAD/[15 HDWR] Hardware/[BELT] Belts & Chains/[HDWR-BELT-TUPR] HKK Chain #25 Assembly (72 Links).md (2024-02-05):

# @
| Attribute | Value |
| ---  | --- |
| Author | SixWingedFreak |
| Date | 09/22/2016 |
| _SW_Last_Saved_With_ | SOLIDWORKS 2024 |
# Default
| Attribute | Value |
| ---  | --- |
| Author | SixWingedFreak |
| Date | 09/22/2016 |

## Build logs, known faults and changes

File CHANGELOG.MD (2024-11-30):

# October 2024 (Released in November)

* Added drawings for finger linkages
* Add drawing for finger hook
* Small tolerance change to the twist pulley cable clamp
* Added drawings for shoulder parts
* Added drawing for neck 8MM D*Shaft
* Added new Track drive Idler Tensioner Assembly
* More rebuild of the lower torso covering
  * Rebuild of entire console section into a main body and magnet attachable side portions
  * A rebuild of the battery frame area where the new door mechs live
  * Split frame area into multiple parts to aid in printing
  * Finished console door mechanism, and mounting blocks
  * Removed duplicate or out of date parts
  * Completed section split and added mounting hardware to lower torso covering
  * Added battery simulate and lugs
  * Updated the pivot point covering to cover the entire metal section
  * Updated Lower toro side plates to add a countersink where the covering mount brackets are
* Updated Goodyear tire with custom design for upcoming manufacturing
* Updated covering mount to align with differing configuring of existing tires
* Added gimbal ring / rod drawings
* Made small adjustments to neck rods and removed some superfluous features
* Added drawings for neck rod ends
* Added 3D printable sleeves for replacement spring spacers
* Modified neck sprocket to match the keyway of the neck rods to minimize the key plate needs
* Added drawing for socket
* Updated the front idler sprocket to use a lock nut instead of a collar
* Small adjustment to the cover plates on the neck rods
* Increased the height of the neck rod potentiometer covering
* Increased the wire passthrough on the neopixel retaining ring in the eye

# July 2024

* Updated neck slide design to a 2-piece 3D print and laser cut design
* Added new Battery Door Mechanism to the Lower Torso Covering (STILL IN ALPHA)
* Added new Console Door Mechanism to Lower Torso Covering (STILL IN ALPHA)
* Updates the the Hand / Finger / Thumb design to use off the shelf pulleys and spacers
* Added new Console Face Plate assembly to work with a new LCD Touchscreen and button design
* Added new Shoulder shaft extension design to eliminate the set screws
* Updated tolerances on Shoulder plates to fit within the laser cut tube (in optimal conditions)
* Updates to arm design (Right arm might not be in sync with left arm) to accommodate fastener and hex standoff adjustments.
* Added a cable sheathing spool spacer to the arm design to prevent the sheathed cables from pushing off the arm covering.
* Small adjustments to the shoulder tube front covering. Extended it down so it hugs the tube better. Added a mount for magnetic attachment. (Still needs a small tweak to prevent collision)
* Added adhesive tape to the Neck C-Channel and opened up the holes in the spring plate
* Added part info to eye vent holding pin

# April 2024 (Released in May)

* Added a number of drawings for arm parts
* Added Left Arm
* Added Flipped configurations of servo cable cages
* Added wire guide for finger cables
* Adjusted the angle of the cable paths for the fingers
* Adjusted finger designs and knobs with inspiration  from work done by Kyle Dedonya
* Switched out finger pulleys for those that can be purchased
* Added a configuration for the cradle base strengthening plate to be used with V2 cradle bases
* Added a series of drawings for hand / arm / wrist parts for production
* Made small adjustments to hand parts in preparation for production
* Added the new V3 Neck Assembly with the 3D printed neck block
* Added a new servo tensioner design and covering
* Material change on Master Cylinder Drive arm

# January 2024 (Released in February)

* Upper Half Speedpack Updates
* Added countersink to track drive accessory plate to avoid PEM protrusion
* Added a small spacer to the EV105 Battery Case for batteries that are shorter than the originals we used to design the case
* Adjustments to the middle torso bushings and plastic spacers
* Changed material callouts for middle torso bent plates
* Small rework of left shoulder (Right shoulder to follow) that makes the metal cuffs easier to laser cut, and the vertical cuff a wire passthrough and a 3D printable part. Also changed the vertical plate’s vertical post width to eliminate the chamfer.
* Added information the the data card for the shoulder bearing.
* Created new 1-Piece neck cup design, and retainer ring.
* Major changes to the tool arm coverings and rear cap. Improved the geometry to make them nest together better, and increased their thickness to .125”.
* Started rework of the tool arm section to create a mounting system for PCBs and accessories to be slot mounted. This section is still incomplete.
* Changed the tubes for the accessory (laser/toolbox) and tool arm to be 3D printed instead of metal, and introduced new aluminum channel to make these sections structurally stable, and altered the mounting method to make these easier to remove.
* Adjusted the cradle base eccentric drive support rod’s hole callout to 1/4-28. Terry thought it was oversized. This change should have minimal impact for anyone who has already made it.
* Moderate adjustments to the upper torso plates, including the removal of the middle plate’s bottom flange, as it served no structural purpose. Changed hole callouts to “close”, and rounded all the sharp corners, punched a big hole through all the plates for wire passthrough and designed a new 3D printed part to aid in wire passthrough that avoids the actuator.
* Exported flat patterns for the changes to the upper torso.
* The upper torso assembly now uses 2 shoulder bolts instead of a through-bolt. This is more like the original design and provides better compression per side.
* Fixed a length error in the Eye Vent pins on the left side, and a configuration error on the right side assembly.
* Started documenting the ASME05B case as it has slight differences to the 04B (Incomplete)
* Added a COMPLETELY NEW V2 version of the Turkey Neck Drive, that can be assembled from 2D laser cut plates.
* Modified the turkey neck sprocket and shafting at the rear of the neck to minimize parts between the shaft and the neck rods. Future versions of the neck rods will be simplified for this design.
* Redesigned the clamping and accessory mounting design for the laser / toolbox. This design uses more off-the-shelf parts, and creates a wiring pass-through for the accessories. More on that in the future.
* Updated the neck cylinder drive to increase the servo arm size and the attachment method.
* Added a new 3D printed “Cable Saver” to allow cables to pass through the tip-toe tube without hitting the edge of the metal tubing. The parts are replaceable without having to take out any wires, if that ever becomes an issue.
* Added to cradle base top covering mount plate out of the work area
* Major work completed on the upper arm. Ready for prototyping. Includes new servo cages for the cabling, and an updated core for wire and pull cable passthrough.
* Small revisions to the shield covering plates and assemblies to allow for left / right configurations and added another magnet spot so the corners stay down.
* Added flat patterns for the caster parts to allow for laser cutting.
* Adjusted tape locations on the cradle base top covering mounts so they are symmetrical.
* Update to the Neck Rod Mount Blocks to prevent collision with the fastener head.

# October 2023 (Released in November)

* Added drawings for the cradle base top and bottom blocks
* Added new 3D printed mounts for cradle base coverings
* Complete rework of the shield coverings into 3 part magnet mounted marvels
* Updates to track drive accessory coverings to use magnet mounts
* Deleted STL exports for the EV105 Case. Export them yourself
* Added flat patterns for the cradle base battery tray
* More progress on the arms, but still not done. Stay tuned
* Added flat pattern for the curved support bracket
* Swapped out the cradle base shaft caps in favor of off the shelf components
* Adjusted the track drive side coverings to be properly symmetrical, and added wire channel cutouts
* Which required minor changes to the outer wire channel
* Added an accessory bundle and mounting plate to the track drives.
* Removed superfluous hole in track tip tube
* Added wire protection design to the track tip spacer
* Added more speedpaks to make large assemblies load faster. Refer to our speedpak video to turn it off.
* Updates to the “Jesus” switch assembly in the middle torso to take the pin out, in favor of a 3D printed feature. Also re-oriented the assembly, because reasons.
* Updated the tie bar assembly and added drawings
* Updated Banana plates to match SendCutSend’s capabilities, and fixed hole sizes in L plates
* Fixed a collision issue with the middle torso pivot bushing
* Updated the lower torso actuator limit mate, as it should never go to 6”
* Finalized the mid torso linkage
* Added a cradle base wire passthrough drill jig template to modify plates that have already been cut

# July 2023 (Released in August)

* Removed lip from lower torso bearing collar to make it laser cuttable
* Added 3D Printable Lower Torso Actuator Support and updated lower torso supports to match
* Change Wollensak lens diaphragm leaf thickness to match actual part
* Added tolerance adjustment features to nose carrier side covering
* Added drawings for V3 PEM version of lower torso
* Fixed broken mates in right eye
* Added drawings for lower torso rod mount, and frame plate
* Added drawing for ID actuator mounting block
* Removed various tolerances on servo arms in the head to account for better 3D printing capabilities.
* Added a middle cutout configuration for the 3D printable nose basket.
* Added drawings for the upper A-Frame plates.
* Updated PEM version of the angled plate to conform with SendCutSend’s abilities.
* Added drawings for 2-piece upper A-Frame bearing cup.
* Updated data plates parts with new design from Andrew.F
* Rebuilt the Upper A-Frame parts into a single part with exports, instead of duplicates.
* Added 3D printable PCB Mounting Assembly to the Upper Torso.
* Modified the Upper Torso side plates to create a stronger, smoother profile.
* Modified 3” Bearing Collar to use binding barrels with the 2-part laser cut version.
* Added drawings for the middle torso cage top and bottom plates.
* Added an entirely new mid-torso linkage assembly intended for bent sheet metal (UNTESTED)
* Added drawings for new A-Frame linkage
* Added a completely new upper torso hinge assembly intended for bent sheet metal, with quick release plate.
* Added drawings for new upper torso hinge assembly.
* Updated the eccentric drive to center the chains, add chain mates, and add shims and spacers to the assembly. Switched materials on some of the spacers to plastic.
* Added new wire passthrough tunnel to the eccentric drive.
* Added new PCB mount plates to the side of the cradle base, with magnet attachment features for the coverings.
* Updated the potentiometer housing and sprocket to make more room for the potentiometer leads.
* Adjusted the Vishay 3-turn potentiometer part to more closely resemble the actual part.
* Fixed mates between the Vishay potentiometer and the housing.
* Added 44 Tooth Sprocket Drill Template for the eccentric drive sprockets, to the Jigs folder.
* Updated the torsion springs in the neck assembly to ones you can actually find at McMaster
* Added a Spring Spacer Plate to the neck assembly to meet the adjusted springs.
* Modified the collar that the neck springs sit in, making the holes tighter, and changing the depth to through holes.
* Modified the diameter of the spring bushing so the new spring doesn’t rock.
* Added new upper torso tip connection bar linkage.
* Added cradle base wire passthrough drill template to modify any existing sheets.

# April 2023

* Added PEM design for Cradle Base and drawings
* Added PEM design for Lower Torso
* Added a new bent strengthening plate for the IDC actuator. Still in prototyping stage. Use with caution.
* Modified the eccentric drive plates to be compatible with the PEM Cradle Base
* Removed the “3D Printable Parts” folder as the parts were not being updated. Export the parts manually to have up to date information.
* Made VexPro configuration the new default for Track Drives, adjusted the chain pattern and adjusted hole locations to match Banebots Heavy Duty motor.
* Added 2-Part lower torso bearing collar
* Re-organized lower torso main structure
* Removed V2 Tip Connection bar
* Created a new 3-piece lower battery box to allow for laser-cutting and bending by SendCutSend
* Added drawings for new 3-piece lower battery box
* Made a minor adjustment to the rear idler axle to prevent hitting the shoulder bolt edge
* Added an export for the uni-chain sprocket
* Added plastic spacer for the front idler to be used with the 3-part idler sprocket
* Added flat patterns for the eccentric drive plates
* Fixed hole features in front idler bushing
* Added drawing for middle torso rotation shaft
* Added rotational cutout in tip connection bar to allow for rotation slop when assembling.
* Begun PEM version of Upper A-frame. Still not complete.
* Adjusted some material callouts for sprocket spacers
* Added keyed shaft configuration to Banebots gearbox for use in the eccentric drive.
* Updated eccentric drive to use Banebots motor which required adjustments to the hex spacers.
* Added metadata to hex spacers to point user to the cheaper vendor.
* Re-exported and configured a bunch of head bottom and top parts. Some upgrade issue broke solid body references.
* Removed magnet feature in curved detail covering in the top left head.
* Changed the eccentric cam material to chromoly for strength, and because it’s available from SendCutSend.
* Added 775 Motor Pinion Installation guide to the Jig’s folder.
* Added new 3D printable tip toe tube spacers, instead of using brass / metal.
* Fixed some lower-half mates in full assembly.

# January 2023

* Updated arm design (Elbow movement only)
* Added a drawing for the tip-toe tube
* Started updating bent parts radius, K-Factor, and material to match SendCutSend’s bending capabilities and our suggested materials
* In certain places, started adding a V3 of bent assemblies to provide a rivet version.
* Added flat pattern file for shield & accessory covering mounting plate
* Added a new 3-piece configuration of the front idler sprocket for cutting by SendCutSend
* Updated front idler to account for new sprocket configuration
* Added a “Complete Assembly” assembly that connects the upper and lower halves.
* Created a 2-piece lower battery box that bending by SendCutSend. This 2 piece is intended for use with rivets.
* Fixed some configuration errors with the rear caster and moved the bearings from the sub assembly up a level, and fixed some mating issues.
* Updated the chest carrier with a new 3-piece bent version to match SendCutSend’s capabilities.
* Added the Lower Torso Covering, including some incomplete work for the battery doors. THIS IS STILL IN PROGRESS
* Added sleeve bearings for the laser cut configuration of the lower a-frame.
* Added a new printable bearing spacer for the shoulder tube
* Added a new track hole link guide to drill holes into track links one at a time with repeatable accuracy.

# July 2022

* Added the new laser cut lower a-frame as a configuration to the lower a-frame assembly.
* Updated the EV105 battery box assembly so it exports the sub parts properly
* Added single piece caster into the caster assembly as a configuration, fixing all references to sub-parts.
* Added 2-Part 3” bearing collar pieces
* Added new Plastruct parts to the repo. Haven’t updated the assemblies that use them yet.
* Added holding pin to eye vent frames in the eye tubes.
* Added some color to the eye frame and vents
* Added a configuration for the adjusted track drive sprocket that reduces bounce
* Added metadata to the flat cable in the tip toe tube
* Added missing fonts to the Fonts directory.
* Fixed a rebuild error in the Hug Motion Assembly
* Fixed a part reference in the K-5-X Master Cylinder assembly
* Fixed reference errors and over definition in upper torso, also rebuilt some speedpaks
* Fixed incorrect fastener size in the upper A-Frame

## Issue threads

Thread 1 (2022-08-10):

Left Neck Cylinder Missing Lower Plate Mounting Screw

Fuelrush, 2022-08-10:
Left Neck Cylinder Missing Lower Plate Mounting Screw. Right cylinder screw selected and shown.

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

Hackmancoltaire, 2022-12-11:
The left and right are just configurations of the same assembly. I'm seeing 3 screws in the `Bottom Ball Mounting Plate Screws` folder. that are visible in both configurations. Check that the parts are in the folder and aren't hidden.
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

Hackmancoltaire, 2022-12-21:
Parts were actually there, just needed to be unsuppressed.

Closed 2022-12-21.

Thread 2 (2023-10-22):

Add fillet on inside of head cover facemask

johnflux, 2023-10-22:
In the file [[HEAD-COVR-MIL1-COMN-01] Facemask.STL](https://github.com/input-inc/OpenSaint/blob/main/J5%20Project/Current%20CAD/3D%20Printable%20Parts/01%20-%20Head/00%20-%20Coverings/%5BHEAD-COVR-MIL1-COMN-01%5D%20Fa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)

There's a sharp right angle on the inside vertical parts. It would be nice if it had a fillet there for strength. Mine broke immediately.

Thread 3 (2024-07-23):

Eye Pop Bolt

Fuelrush, 2024-07-23:
The bolt that holds [HEAD-J-C-01] Arm onto the 6mm lead screw nut is spec'd too long.

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

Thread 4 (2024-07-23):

Resin Ball Description Wrong Size

Fuelrush, 2024-07-23:
The description of the .375" resin ball in [HEAD-B-D-COMN-01] Frame is showing .5"

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

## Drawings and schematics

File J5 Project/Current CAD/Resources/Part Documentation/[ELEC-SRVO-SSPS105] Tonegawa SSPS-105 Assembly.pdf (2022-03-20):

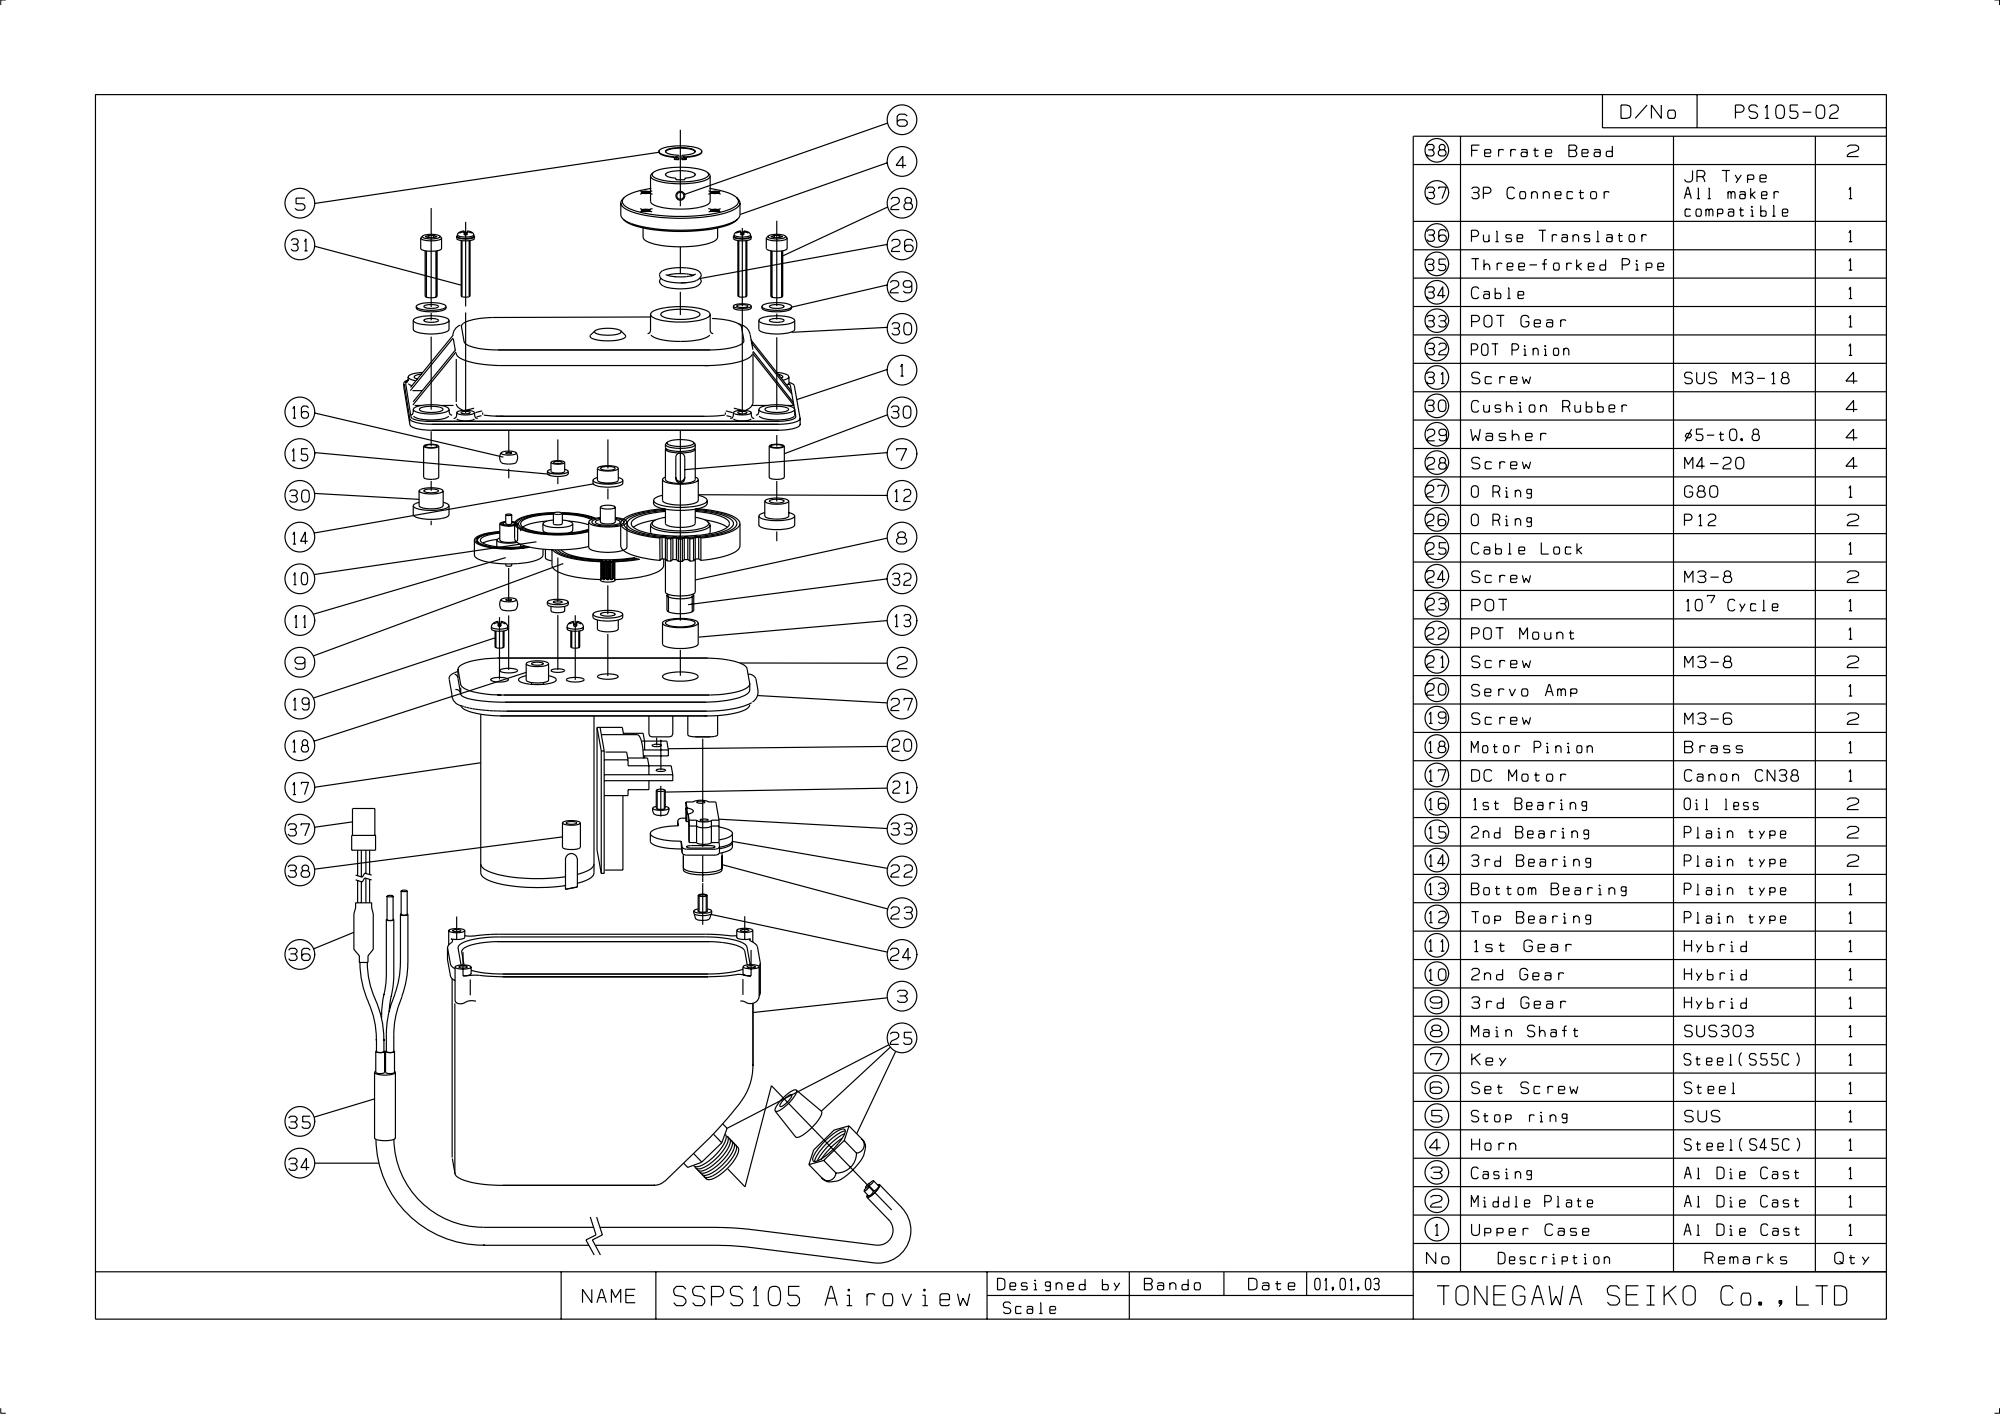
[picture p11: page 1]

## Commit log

2022-03-20 First release of the public OpenSAINT CAD
    [Input-Inc Cut List.xlsx, Input-Inc Sheet Format.SLDDRW, Lip Light LED Holder.stl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]
2022-07-17 OpenSAINT Release: release-202207162303
    [[AFRM-LWR-COMN-V2-00] Rod Mount.SLDPRT, [AFRM-LWR-COMN-V2-01] Side Rod Mount.SLDPRT, [AFRM-LWR-COMN-V2-03] Frame Plate.SLDPRT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]
2023-01-07 OpenSAINT Release: release-202301062126
    [Flat-Pattern - [TDRV-COMN-06] Shield & Accessory Covering Mounting Plate.DWG, [AFRM-LWR] Lower A-Frame.SLDASM, [ARM-A-V2-LEFT] Shoulder (Left).SLDASM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]
2023-04-12 OpenSAINT Release: release-202304121019
    [Flat-Pattern - [CRDL-V3-A-01] Bottom Plate.DXF, [AFRM-UPR-V2-A-00] Side Plate.SLDPRT, [AFRM-UPR-V2-A-02] Bottom Plate.SLDPRT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]
2023-08-13 OpenSAINT Release: release-202308122315
    [SAINT Data Plate (Andrew Edit).dxf, [AFRM-LWR-COMN-V2-00] Rod Mount.DWG, [AFRM-LWR-COMN-V2-01] Side Rod Mount.DWG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]
2023-11-19 OpenSAINT Release: release-202311182311
    [[AFRM-LWR] Lower A-Frame.SLDASM, [AFRM-UPR] Upper A-Frame.SLDASM, [ARM-B-COMN-06] D-Shaft Pulley Mount.SLDPRT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]
2024-02-05 OpenSAINT Release: release-202402041821
    [[ARM-A-V2-COMN-00] Mounting Plate.SLDPRT, [ARM-A-V2-COMN-02] Spring Shaft.SLDPRT, [ARM-A-V2-COMN-INNR-COMN-00] Inner Cuff.SLDPRT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]
2024-05-26 OpenSAINT Release: release-202405252359
    [Tube-125X035_2-Tube_1-[TUPR-D] Master Cylinder Drive.sldprt, Tube-125X035_3-Tube_1-[TUPR-D] Master Cylinder Drive.sldprt, Tube-125X035_4-Tube_1-[TUPR-D] Master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]
2024-07-29 OpenSAINT Release: release-202407282024
    [[ARM-A-V2-COMN-00] Mounting Plate.SLDDRW, [ARM-A-V2-COMN-00] Mounting Plate.SLDPRT, [ARM-A-V2-COMN-04] Spring Cover Plate.SLDDRW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]
2024-11-30 OpenSAINT Release: release-202411291907
    [[ARM-A-V2-COMN-05] Servo Shaft Interface.DWG, [ARM-A-V2-COMN-08] Key Plate.DWG, [ARM-B-LEFT-A-INNR-00] Side Plate (Left, Inner).SLDPRT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]
